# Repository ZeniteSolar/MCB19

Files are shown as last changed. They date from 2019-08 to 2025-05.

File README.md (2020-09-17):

# MCB19






**M**ódulo **C**arregamento das **B**aterias 2019 

Embarcação Guarapuvu II

Equipe Zênite Solar

### LICENSES

- All firmware (unless otherwise noted), [is licensed under GPL-3.0 or any later version](https://www.gnu.org/licenses/gpl.html)
- All hardware is [licensed under CERN-OHL-S v2 or any later version](https://ohwr.org/cern_ohl_s_v2)

### Sobre

Este módulo é responsável por carregar e gerenciar a carga da bateria auxiliar (rádio e bombas de porão) e da bateria extra (direção elétrica) a partir da energia da bateria principal.

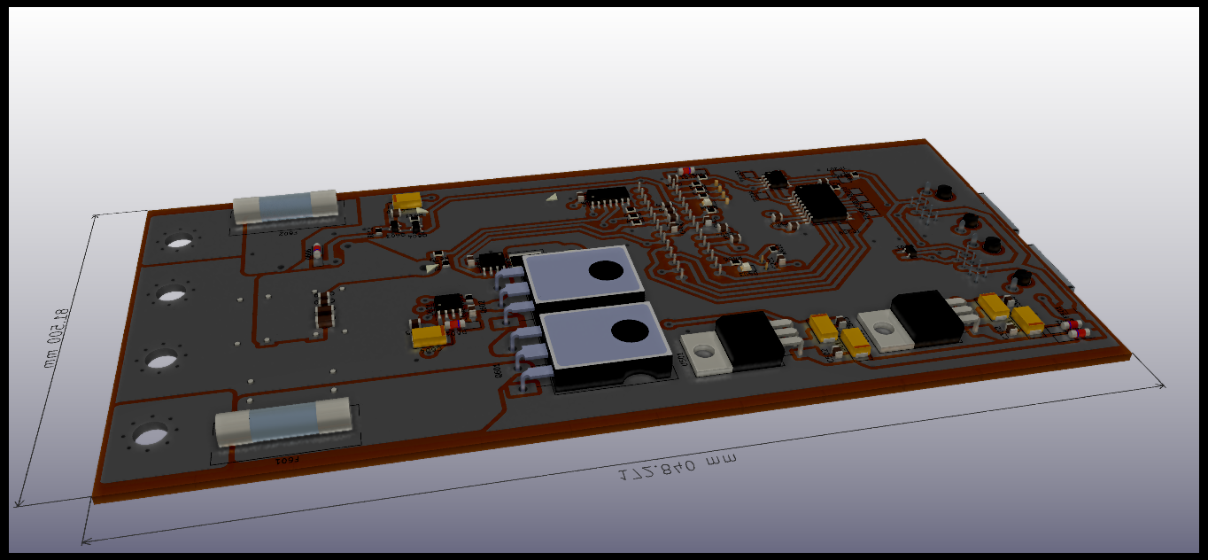
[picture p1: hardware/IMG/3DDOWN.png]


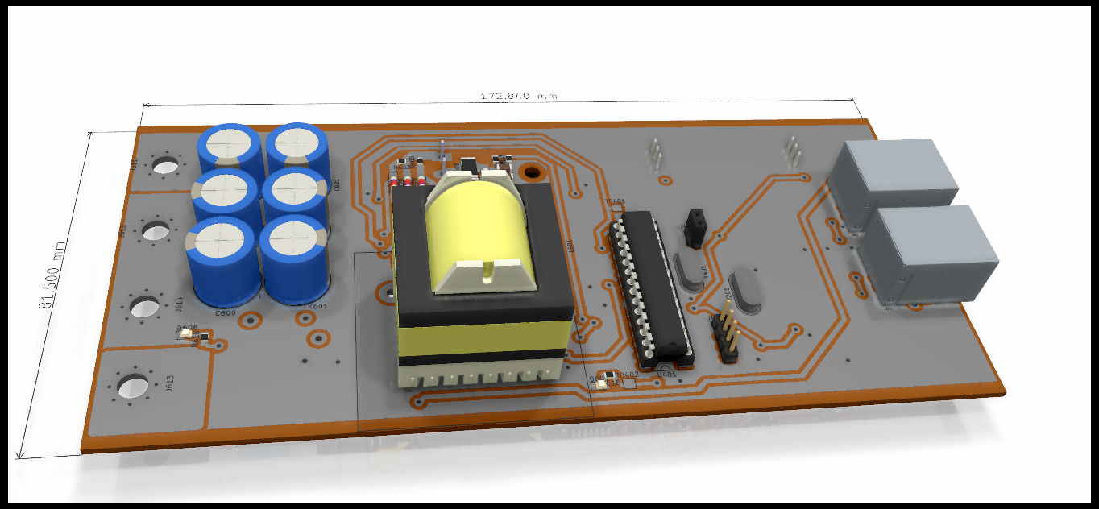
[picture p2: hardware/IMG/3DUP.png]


#### Requisitos

1. Carregar a bateria

   - Carregar por CC e CV
      - Controlar a tensao com controlador PI em cascata com controlador PI de corrente.

   - Proteções
      - Sobrecorrente na entrada e saída
      - Curto-circuito na entrada e saída
      - Sobre/sub-tensão na entrada e saída
      - Não permitir corrente da saída para a entrada: Um relé em série com a carga é usado para permitir a leitura da tensão na saída antes de entregar corrente para ela, seguindo as seguintes regras:
        - Somente ligar o relé da saída quando o sistema estiver em regime (sem oscilações na entrada ou na saída).
        - Somente ligar o relé da saída quando a tensão na bateria estiver em niveis dentro do esperado. 

2. Monitoramento do estado das baterias

   - Enviar pela rede CAN:
      - Corrente de carga
      - Tensão da bateria
      - Tensão da bateria principal
### Abordagens

 1. Especificação do conversor
   - Tensão de entrada: 30-50V
   - Corrente de saida: 8A
   - Tensão de saida: 10-15V

   Como no sistema, a tensão da bateria principal (entrada) será sempre maior que a tensão a tenão da bateria extra/auxiliar (saída), foi escolhido projetar um conversor estatico CC-CC Buck, com chaveamento síncrono (dois mosfets) para maior obter eficiencia.
   #### [Projeto do Buck](https://github.com/ZeniteSolar/MCB19/blob/master/control/buck.ipynb)
   
   - Para as condições especificadas anteriormente foram escolhidos:
      - Capacitor de saida: 200uF
      - Indutor de saida 300uH
 2. Controlador
   - Por sua simplicidade de implementação e por permitir ajustes empíricos, controladores PI foram escolhidos para controlar tanto a tensão de saída quanto a corrente de saída.
   
   [Referencia](https://e2e.ti.com/cfs-file/__key/communityserver-discussions-components-files/902/PI-controller-equations.pdf)
 
 3. Simulações
   - Para a simulação foi usado o programa Psim pois ele oferece a simulação de bloco C onde foi possivel simular de uma forma simplificada o comportamento do atmega328p, alem de ter ferramentas para controle.

<table width="100%">
  <tr>
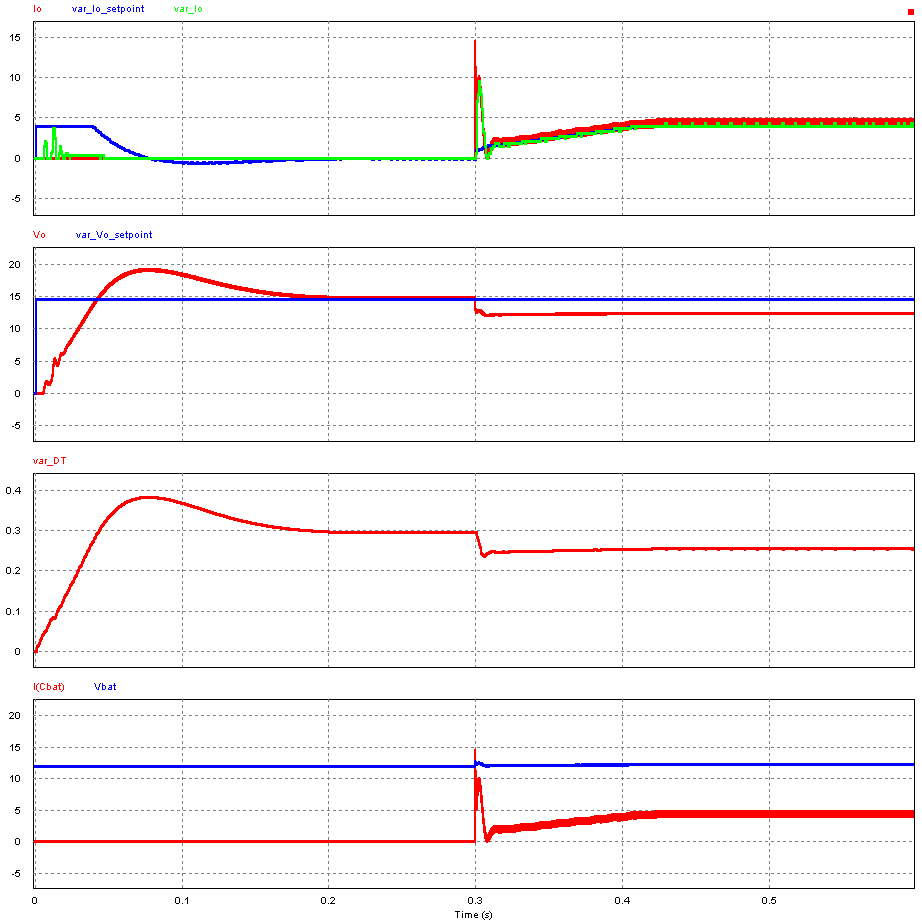
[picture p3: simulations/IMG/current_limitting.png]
    <th width="35%"> </th>
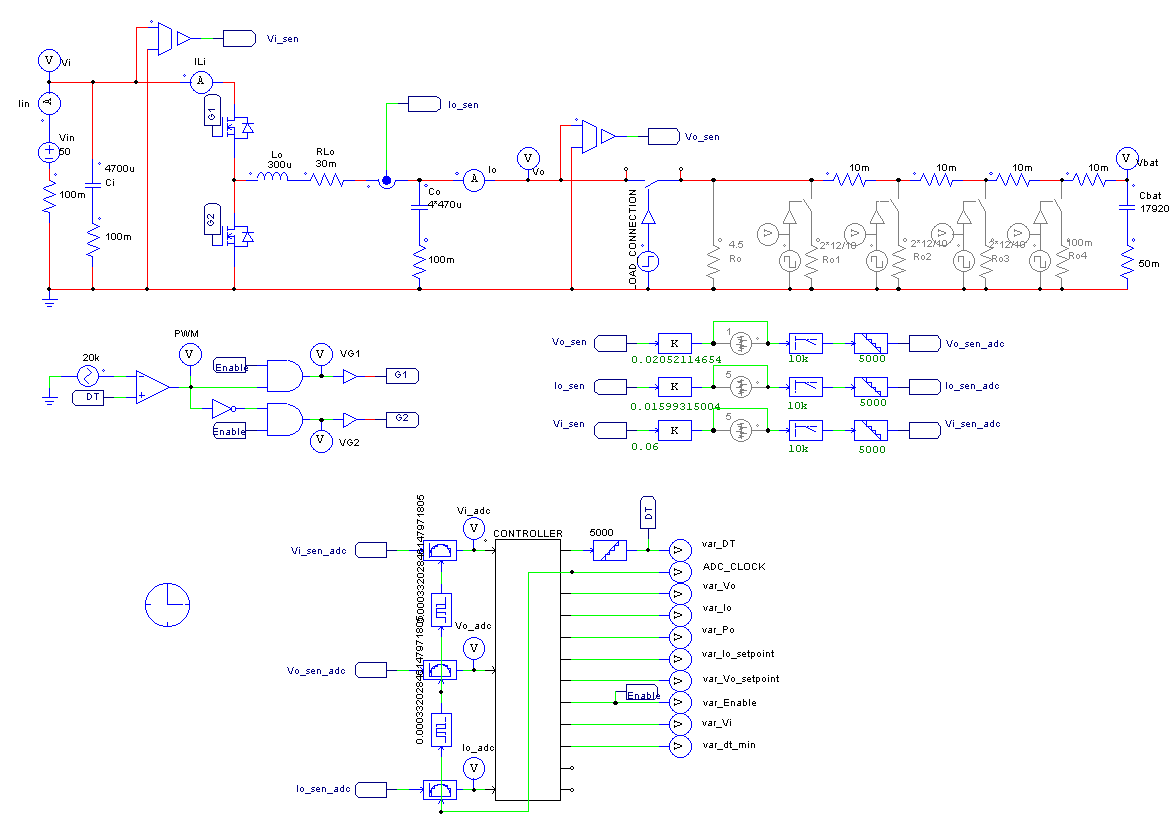
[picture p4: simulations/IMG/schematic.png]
    <th width="65%"></th>
  </tr>
</table>

   4. Hardware
   - Para o design da Placa de circuito impresso (PCB) foi utilizado o software KiCad por ser uma ferramenta OpenSource. A PCB foi fabricada usando transferencia termica.
   
   #### É importante a utilização de snubber para amortecer os picos de tensão nas chaves
   
   5. Firmware
   - A cada interrupção do ADC é chamada a função de controle. Ao finalizar a maquina de estados é executada onde as mensagens CAN são enviadas e recebidas.
   
### [src/conf.h](firmware/src/conf.h)

Configurações gerais do sistema
```C
//#Definições do conversor
#define VO_SETPOINT 	13.2
#define IO_MAX      	8
#define VI_MIN      	21
```
### [src/adc.c](firmware/src/adc.c)
   No arquivo adc.c são lidos os valores dos ADCs e convertidos a valores "humanos", tambem é chamada a função de controle
   - Coeficientes de linearização
      - Com estes coeficientes é convertido o valor lido pelo ADC em uma unidade de medida 
```C
    static const float vi_coeff = 0.06582490575070313f;                                         
    static const float vo_coeff = 0.06717781789490249f;                          
    static const float io_coeff = 0.01599315004f; 
```
### [src/control.c](firmware/src/control.c)
   No arquivo control.c é executado o algoritmo de controle (PiVo em cascata com PiIo), para sintonizar o controlador tem que mudar as constantes Kp e Ti

```C

/*          PI CONTROL ALGORITHM - SERIES IMPLEMENTATION
** /desc    Algoritimo para Controlador Proporcional Integrativo Diferencial.
**  ref1: 
https://e2e.ti.com/cfs-file/__key/communityserver-discussions-components-files/902/PI-controller-equations.pdf

** /var r é o valor desejado para a saída, o 'set-point'.
** /var y é o valor da saída.
** /ret     retorna a ação de controle u.
*/
inline float piVo(float r, float y){
    // PI CONFIGURATIONS:
    const float Kp = 0.5;           // analog series proportional gain
    const float Ti = 0.1;          // analog series integration period
    const float Ts = PERIOD;        // digital sampling period

    // INTERNAL CONSTANTS COMPUTATION:
    const float a0 = -Kp;           // IIR coefficient for old sample
    const float a1 = Kp*(1+Ts/Ti);  // IIR coefficient for new sample

    // CONTROLLER STATIC VARIABLES
    static float e0 = 0;            // old error
    static float e1 = 0;            // new error
    static float u = 0;             // control action

    // Compute error:
    e0 = e1;
    e1 = r -y;

    // Compute control action:
    u += + a1*e1 + a0*e0;

    return u;
}

inline float piIo(float r, float y){
    // PI CONFIGURATIONS:
    const float Kp = 0.001;         // analog series proportional gain
    const float Ti = 0.001;         // analog series integration period
    const float Ts = PERIOD;        // digital sampling period

    // INTERNAL CONSTANTS COMPUTATION:
    const float a0 = -Kp;           // IIR coefficient for old sample
    const float a1 = Kp*(1+Ts/Ti);  // IIR coefficient for new sample

    // CONTROLLER STATIC VARIABLES
    static float e0 = 0;            // old error
    static float e1 = 0;            // new error
    static float u = 0;             // control action

    // Compute error:
    e0 = e1;
    e1 = r -y;

    // Compute control action:
    u += + a1*e1 + a0*e0;

    // Anti windup
    if(u < D_MIN)           u = D_MIN;
    else if(u > D_MAX)      u = D_MAX;

    return u;
}
```
### [src/machine.c](firmware/src/control.c)
   No arquivo machine.c é executada a maquina de estados

```C
inline void machine_run(void)                                                    
{                                                                                   
    if(print_adc){ print_infos(); print_adc = 0;}                                   
                                                                                    
    if(machine_clk){                                                                
        machine_clk = 0;                                                            
                                                                                    
        if(error_flags.all){                                                        
            print_system_flags();                                                   
            print_error_flags();                                                    
            print_infos();                                                          
            set_state_error();                                                      
        }                                                                           
                                                                                    
        switch(state_machine){                                                      
            case STATE_INITIALIZING:                                                
                task_initializing();                                                
                                                                                    
                break;                                                              
            case STATE_IDLE:                                                        
                task_idle();                                                                    
                                                                                    
                break;                                                              
            case STATE_RUNNING:                                                     
                task_running();                                                     
                #ifdef CAN_ON                                                       
                    can_app_task();                                                 
                #endif /* CAN_ON */                                                 
                                                                                    
                break;                                                              
            case STATE_ERROR:                                                       
                task_error();                                                       
                                                                                    
            case STATE_RESET:                                                       
            default:                                                                
                task_reset();                                                       
                break;                                                              
        }                                                                           
    }                                                                               
}                
```

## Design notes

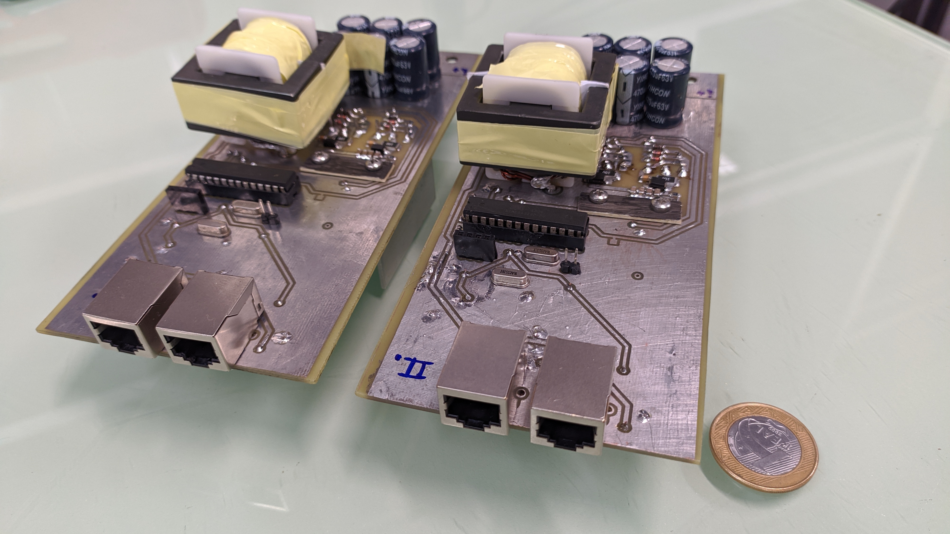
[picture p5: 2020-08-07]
hardware/IMG/PlacaMontada_3.jpg

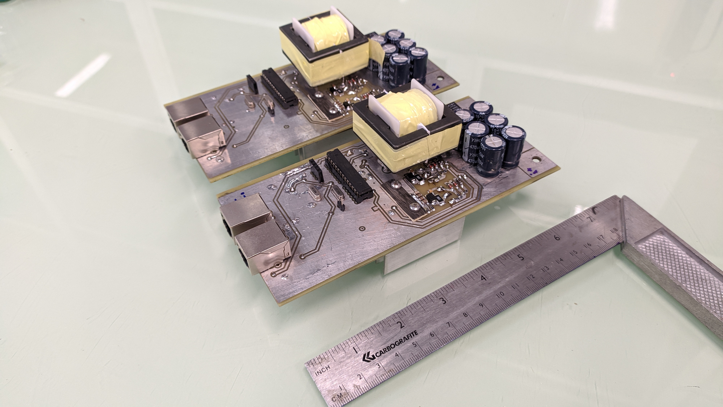
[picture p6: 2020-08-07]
hardware/IMG/PlacaMontada_2.jpg

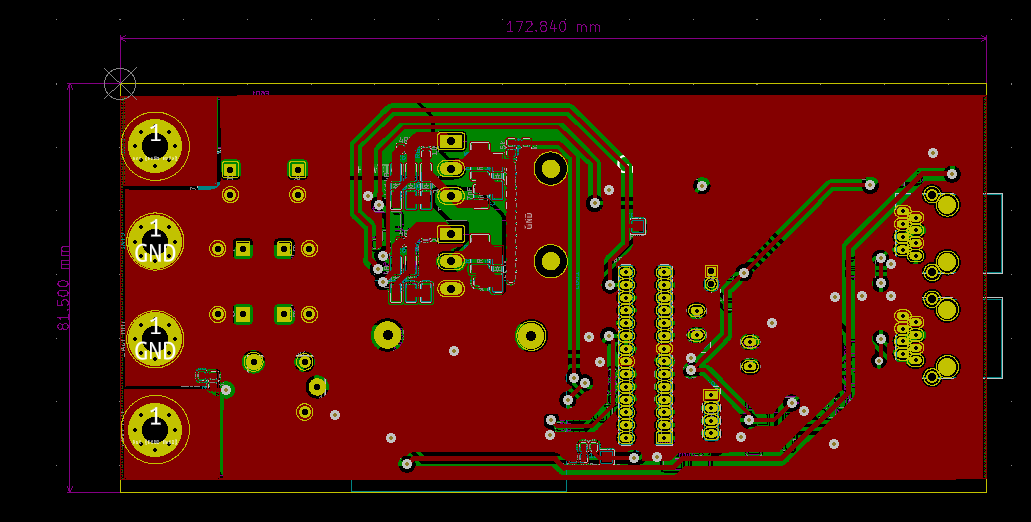
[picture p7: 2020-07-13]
hardware/IMG/layouttop.png

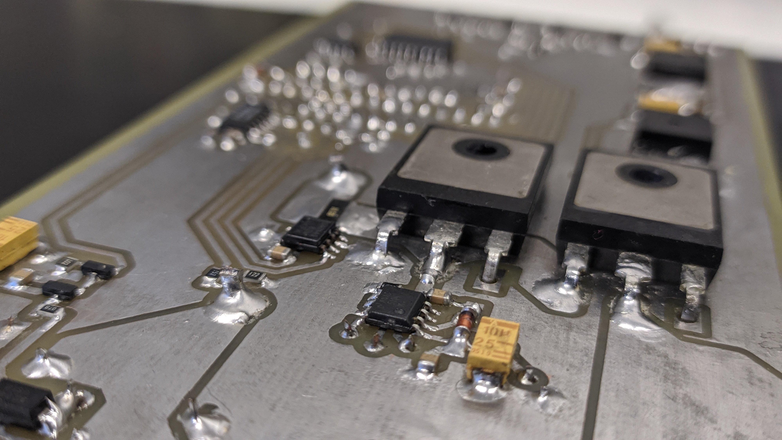
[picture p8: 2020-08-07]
hardware/IMG/PlacaMontadaemdetalhe_DRIVEREMOSFET.jpg

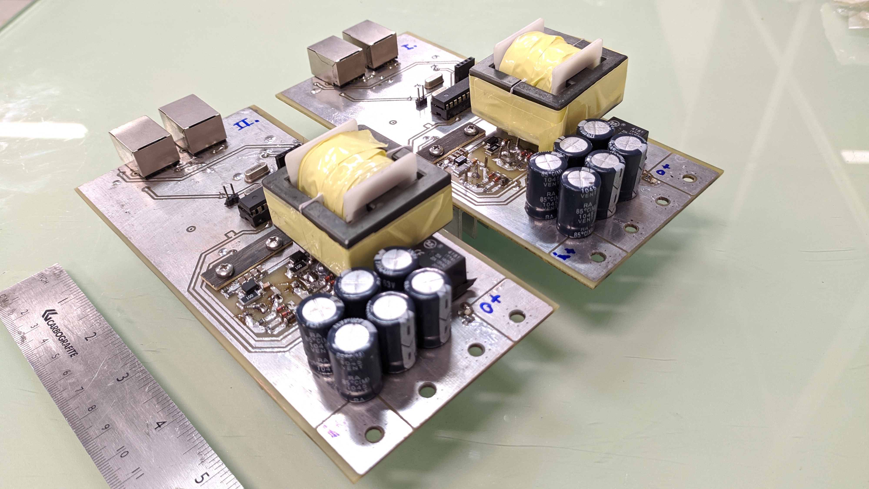
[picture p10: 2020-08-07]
hardware/IMG/PlacaMontada.jpg

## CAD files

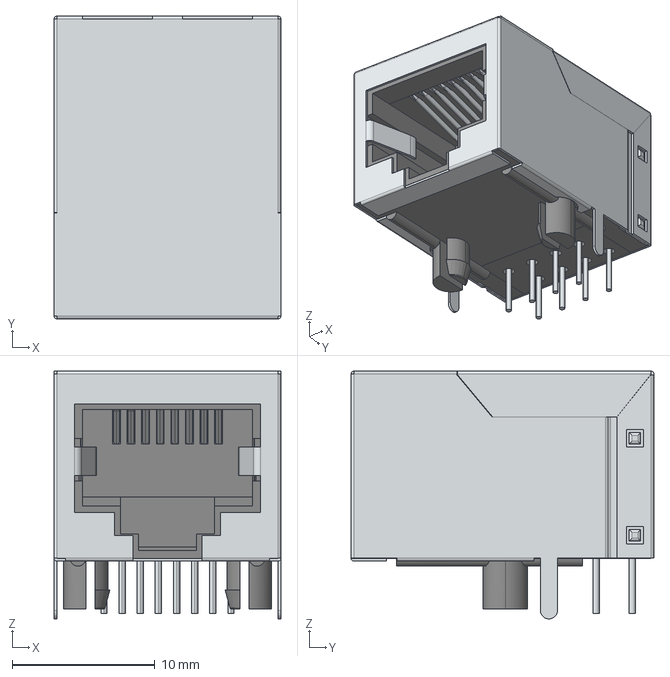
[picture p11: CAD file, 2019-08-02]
hardware/rj45.step
15.9 x 21.2 x 17.3 mm

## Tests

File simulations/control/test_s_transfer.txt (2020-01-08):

C:\users\joaoantoniocardoso\Desktop\ZeniteSolar\2019\MCB19\simulations\control\test_s
C:\users\joaoantoniocardoso\Desktop\ZeniteSolar\2019\MCB19\simulations\control\test_s_param.txt
Loop type = Double
Outer loop = voltage divider + PI
Inner loop = current sensor + PI
Export option = sdomain
Get = Regulator and parameters

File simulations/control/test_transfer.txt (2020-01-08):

C:\users\joaoantoniocardoso\Desktop\ZeniteSolar\2019\MCB19\simulations\control\test.psimsch
C:\users\joaoantoniocardoso\Desktop\ZeniteSolar\2019\MCB19\simulations\control\test_param.txt
Loop type = Double
Outer loop = voltage divider + PI
Inner loop = current sensor + PI
Export option = components
Get = Only parameters

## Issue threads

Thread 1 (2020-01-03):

PWM pin

guilhermecv, 2020-01-03:
Alterar pino do PWM, atualmente no PC5

joaoantoniocardoso, 2020-01-08:
Nesse protótipo está no PB2, mas ainda não foi alterado no esquemático e layout.

Closed 2020-01-22.

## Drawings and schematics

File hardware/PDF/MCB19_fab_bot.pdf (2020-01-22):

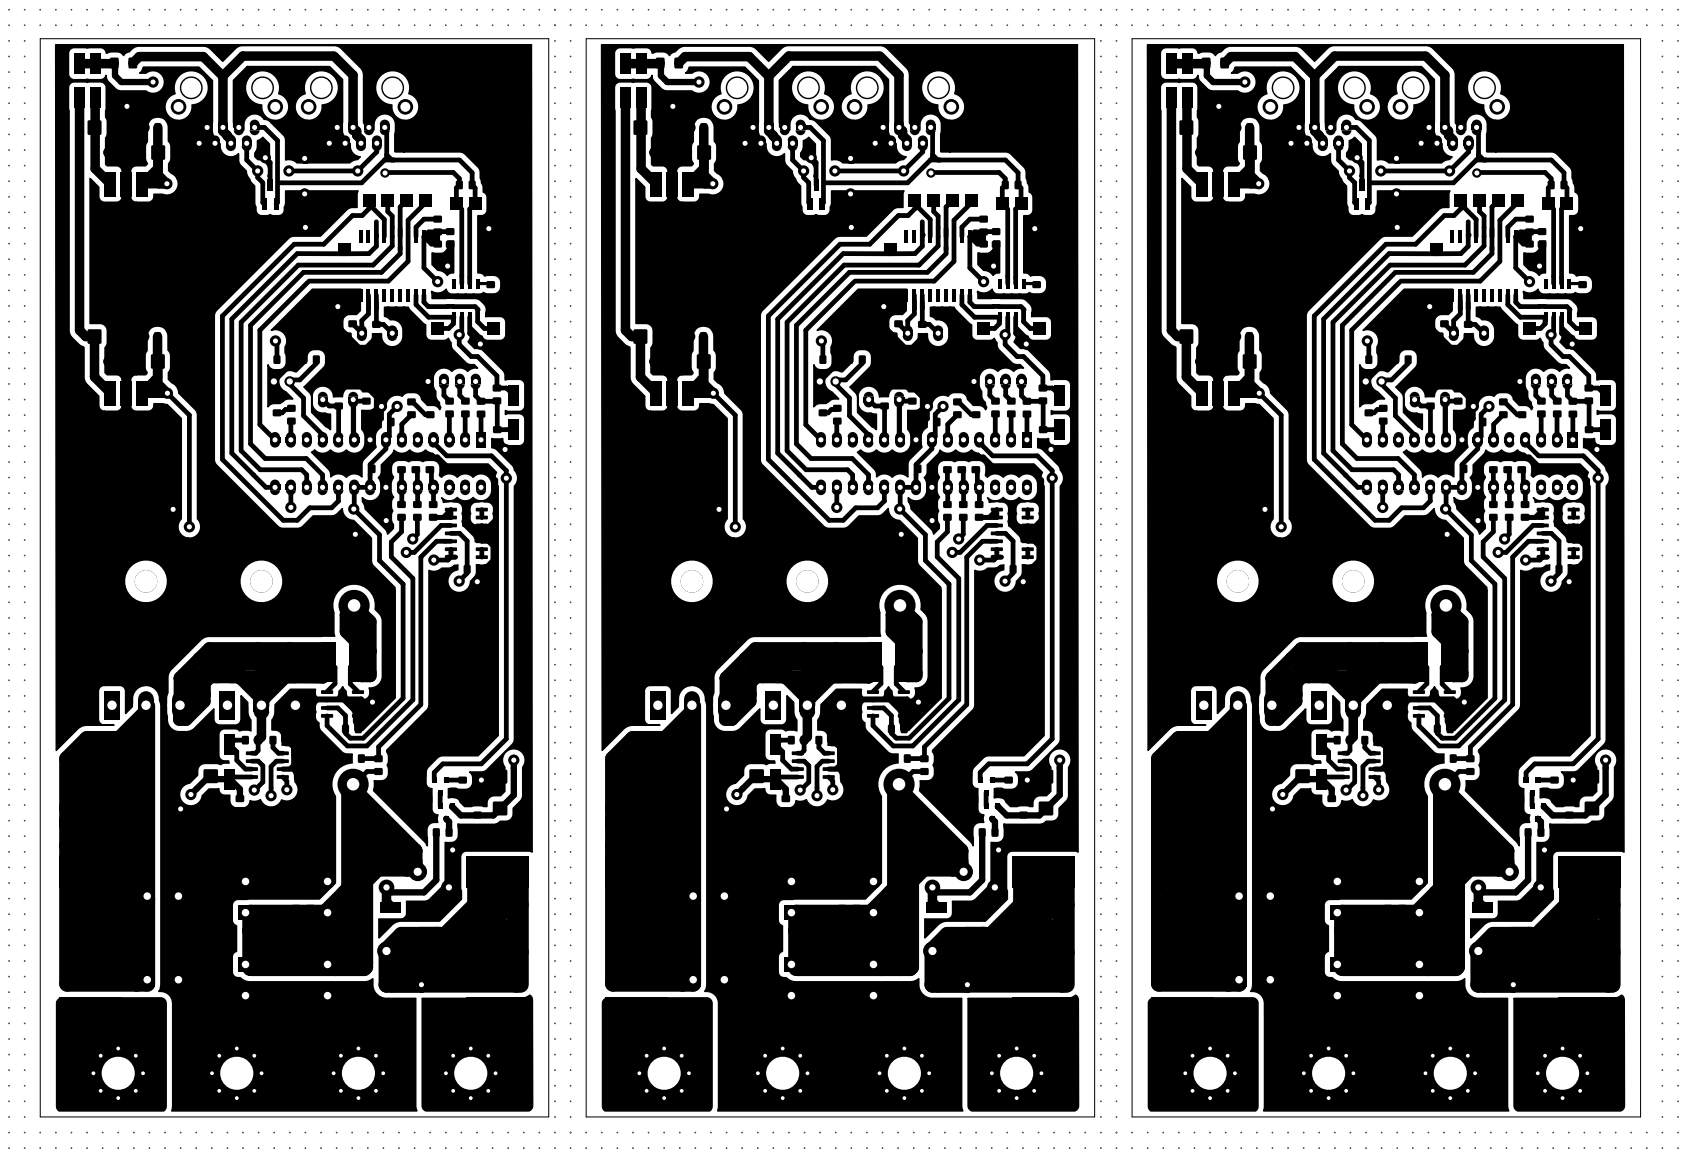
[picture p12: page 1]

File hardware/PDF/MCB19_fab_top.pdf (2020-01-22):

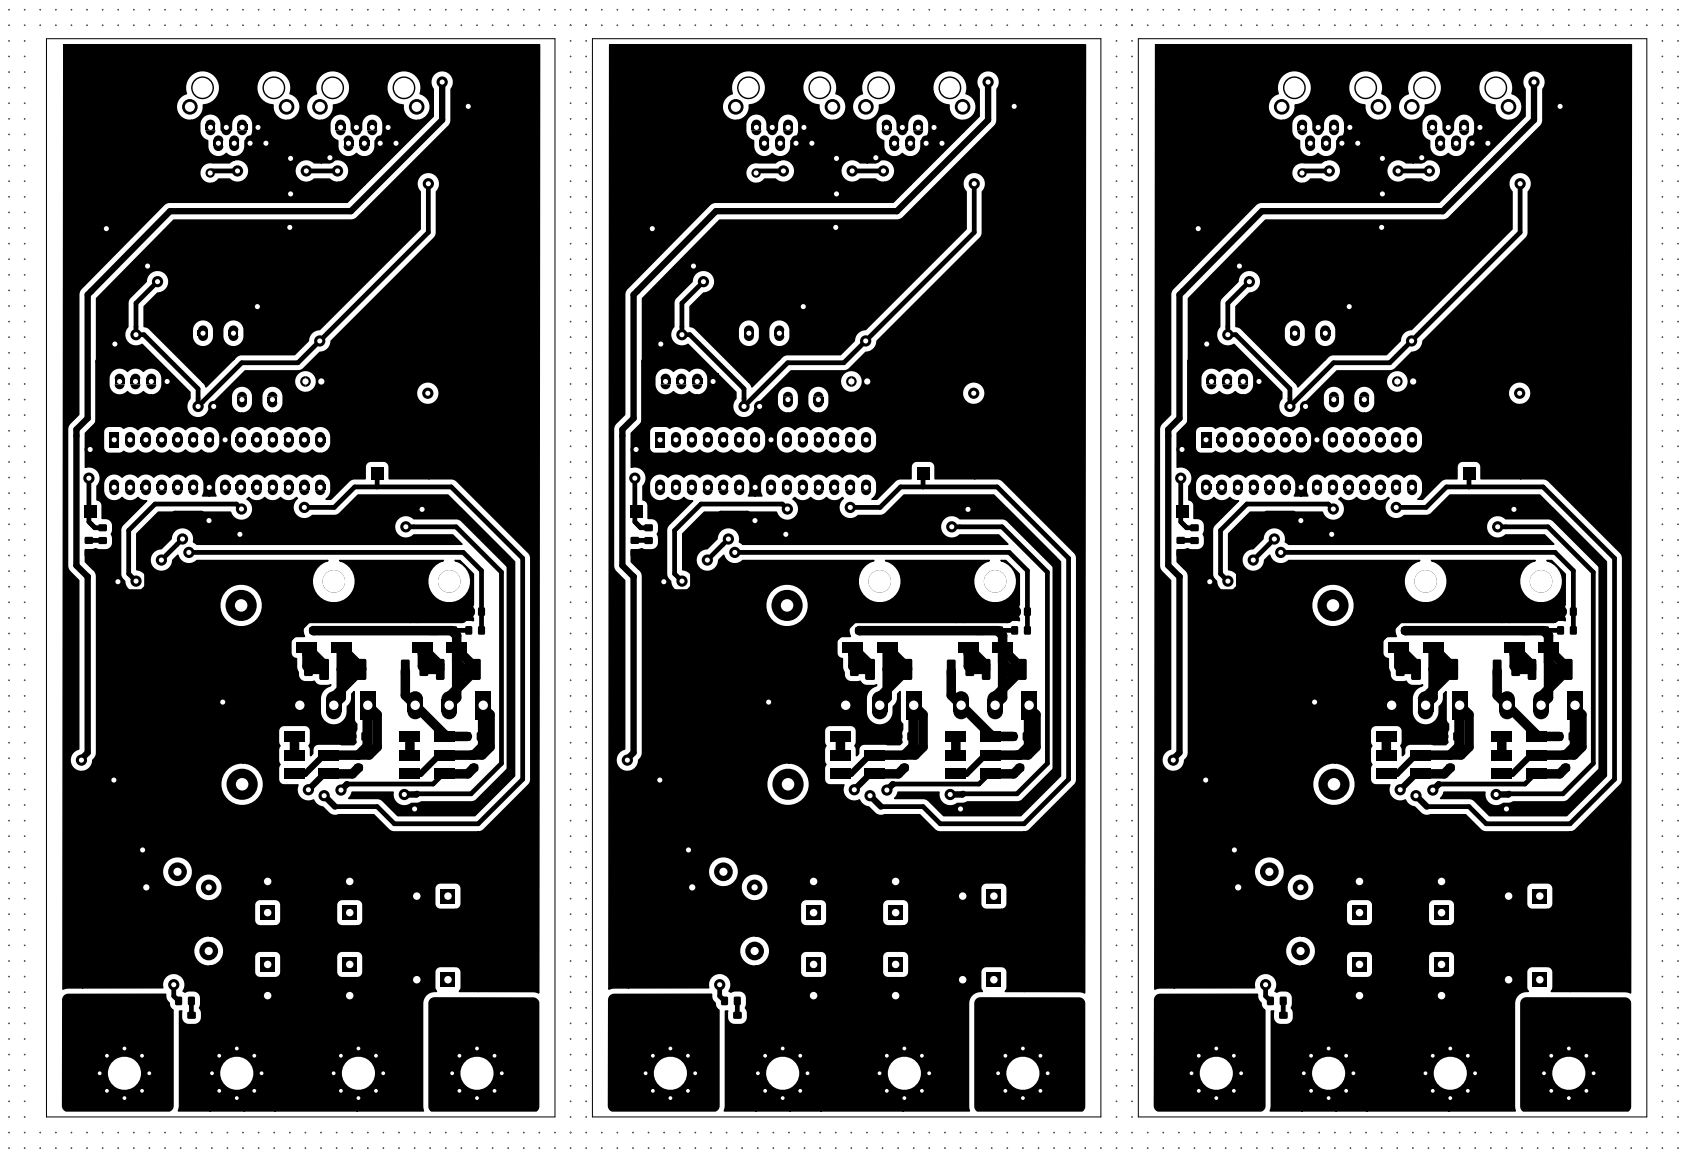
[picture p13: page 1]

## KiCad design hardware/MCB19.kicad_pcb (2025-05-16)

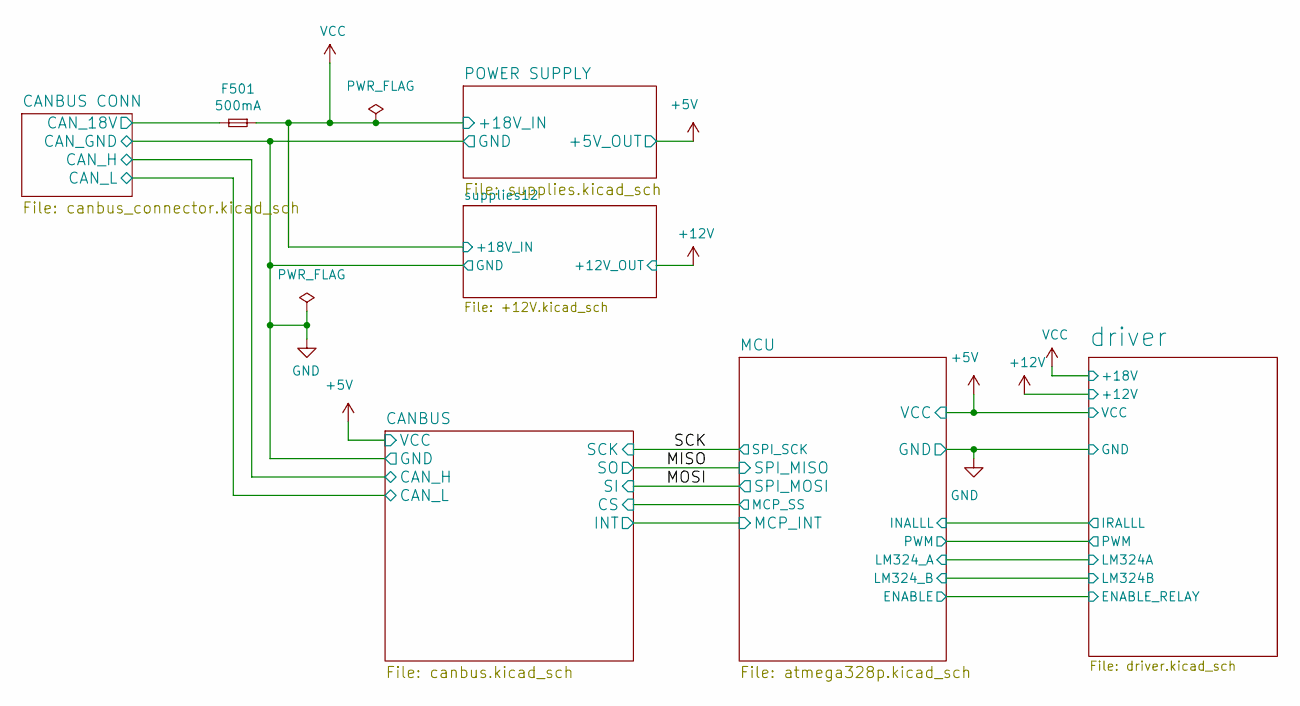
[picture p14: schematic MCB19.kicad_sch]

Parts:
F501: 500mA; Fuse_1206_3216Metric_Pad1.42x1.75mm_HandSolder

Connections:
/CANBUS CONN/CAN_18V: F501.2; also elsewhere on the board
VCC: F501.1; also elsewhere on the board

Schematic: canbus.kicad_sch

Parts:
C201, C202, C205: 100nF; C_0805_2012Metric_Pad1.15x1.40mm_HandSolder
C203, C204: 22pF; C_0805_2012Metric_Pad1.15x1.40mm_HandSolder
D201: pesd1can; SOT-23_Handsoldering
R201: 1k; R_0805_2012Metric_Pad1.15x1.40mm_HandSolder
R202: 4k7; R_0805_2012Metric_Pad1.15x1.40mm_HandSolder
R203: 10k; R_0805_2012Metric_Pad1.15x1.40mm_HandSolder
TP201: SI; TestPoint_Pad_2.0x2.0mm
TP202: SO; TestPoint_Pad_2.0x2.0mm
TP203: TXCAN; TestPoint_Pad_2.0x2.0mm
TP204: RXCAN; TestPoint_Pad_2.0x2.0mm
TP205: SC; TestPoint_Pad_2.0x2.0mm
TP206: SCK; TestPoint_Pad_2.0x2.0mm
TP207: CAN_H; TestPoint_Pad_2.0x2.0mm
TP208: CAN_L; TestPoint_Pad_2.0x2.0mm
TP209: INT; TestPoint_Pad_2.0x2.0mm
U201: MCP2551-I/SN; SOIC-8_3.9x4.9mm_P1.27mm
U202: MCP2515-xSO; SOIC-18W_7.5x11.6mm_P1.27mm
Y201: 16MHz; Crystal_HC49-U_Vertical

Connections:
+5V: C201.1, C202.1, C205.1, R203.1, U201.3 (VDD), U202.18 (VDD); also elsewhere on the board
/CANBUS CONN/CAN_H: D201.1, R201.2, TP207.1, U201.7 (CANH); also elsewhere on the board
/CANBUS CONN/CAN_L: D201.2, R201.1, TP208.1, U201.6 (CANL); also elsewhere on the board
/CANBUS/RXCAN: TP204.1, U201.4 (RXD), U202.2 (RXCAN)
/CANBUS/TXCAN: TP203.1, U201.1 (TXD), U202.1 (TXCAN)
/MCU/MCP_INT: TP209.1, U202.12 (~INT); also elsewhere on the board
/MCU/MCP_SS: TP205.1, U202.16 (~CS); also elsewhere on the board
/MISO: TP202.1, U202.15 (SO); also elsewhere on the board
/MOSI: TP201.1, U202.14 (SI); also elsewhere on the board
/SCK: TP206.1, U202.13 (SCK); also elsewhere on the board
unnamed: R202.1, U201.8 (STBY)
unnamed: C204.1, U202.8 (OSC1), Y201.2
unnamed: C203.1, U202.7 (OSC2), Y201.1
unnamed: R203.2, U202.17 (~RESET)

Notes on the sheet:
EMI/ESD Protection Solutions for the CAN Bus: https://www.onsemi.com/pub/Collateral/AND8169-D.PDF SparkFun CAN-Bus Shield: https://cdn.sparkfun.com/datasheets/Dev/Arduino/Shields/SparkFun_CAN-Bus_Shield_v13a.pdf

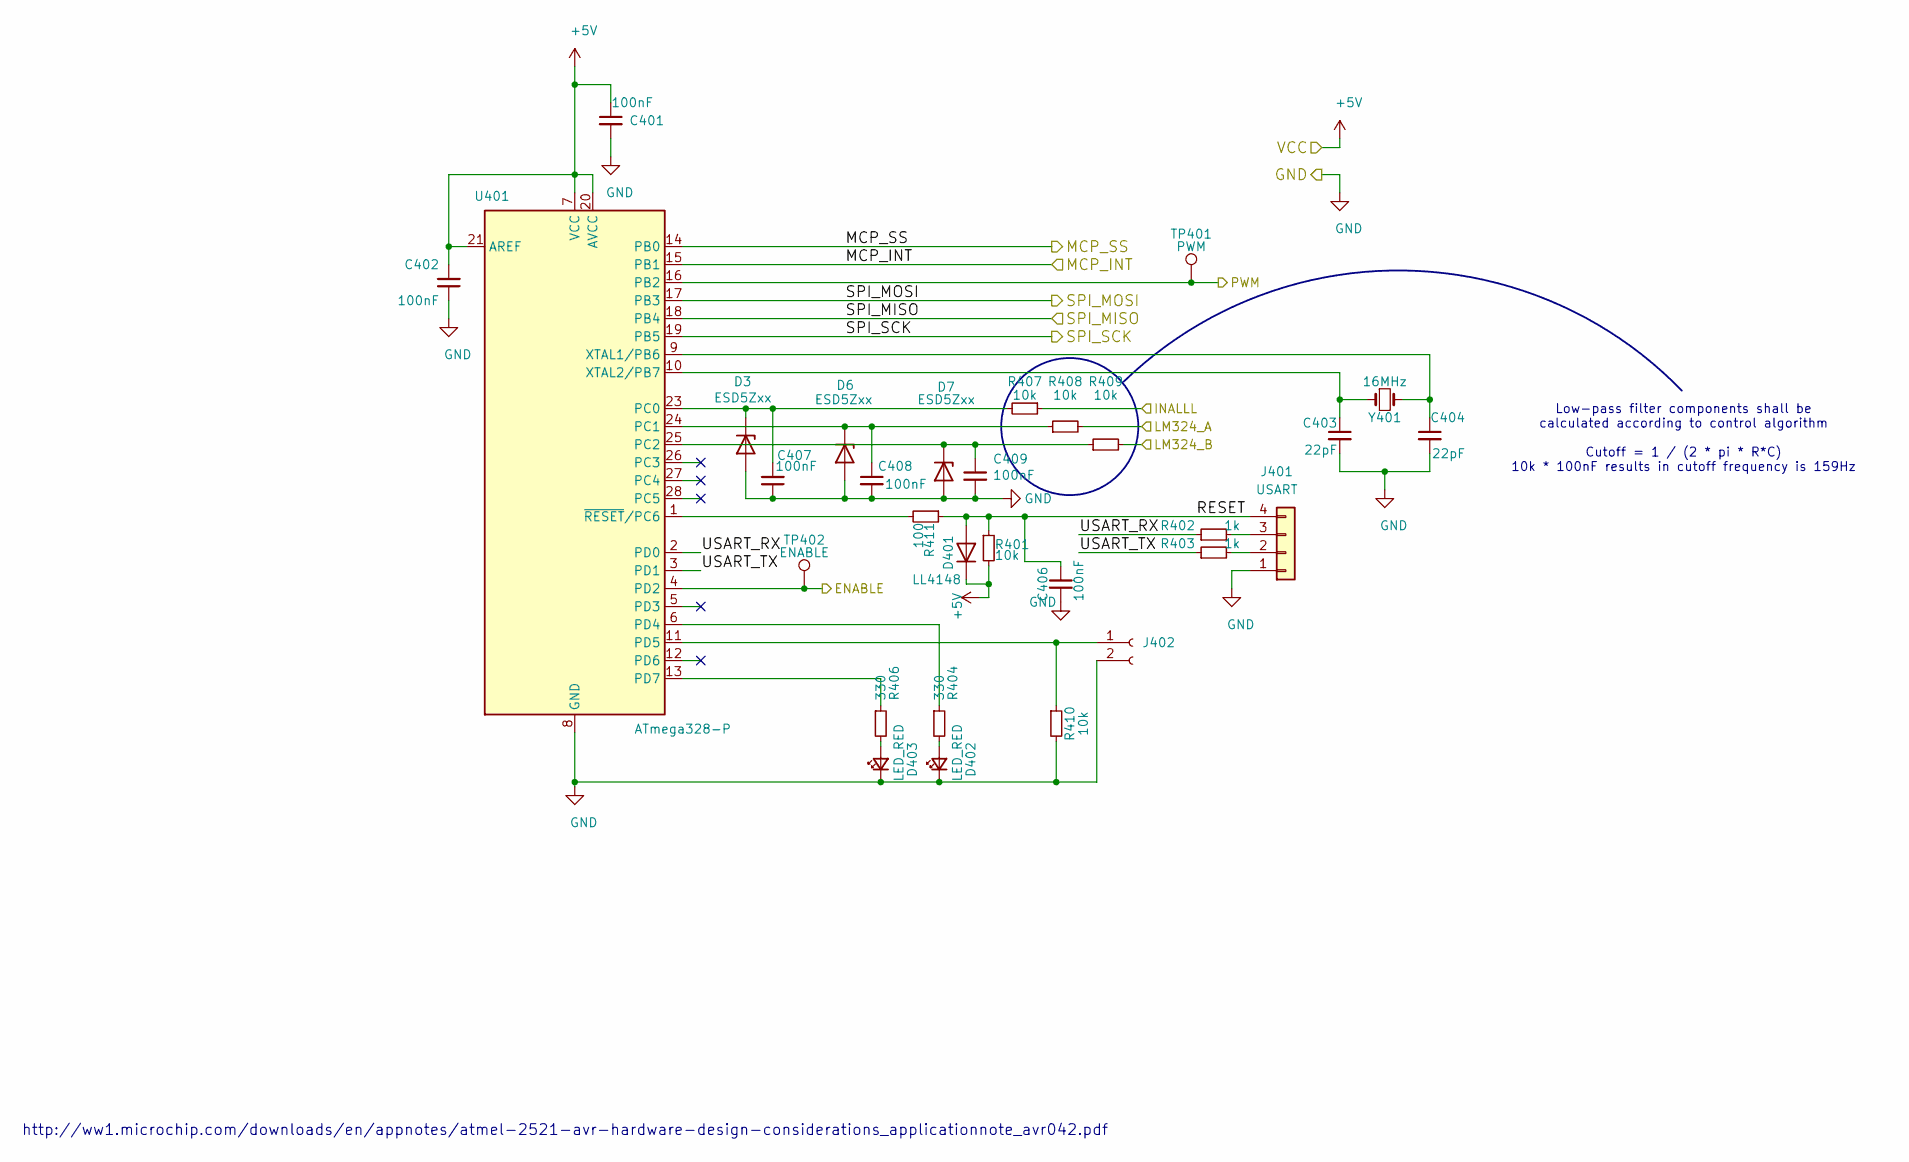
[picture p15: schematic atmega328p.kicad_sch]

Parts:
C401, C402, C406, C407, C408, C409: 100nF; C_0805_2012Metric_Pad1.15x1.40mm_HandSolder
C403, C404: 22pF; C_0805_2012Metric_Pad1.15x1.40mm_HandSolder
D3, D6, D7: ESD5Zxx; D_SOD-523
D401: LL4148; D_MiniMELF_Handsoldering
D402, D403: LED_RED; LED_0805_2012Metric_Pad1.15x1.40mm_HandSolder
J401: USART; PinHeader_1x04_P2.54mm_Vertical
J402: Conn_01x02_Socket; PinSocket_1x02_P2.54mm_Vertical
R401, R407, R408, R409, R410: 10k; R_0805_2012Metric_Pad1.15x1.40mm_HandSolder
R402, R403: 1k; R_0805_2012Metric_Pad1.15x1.40mm_HandSolder
R404, R406: 330; R_0805_2012Metric_Pad1.15x1.40mm_HandSolder
R411: 100; R_0805_2012Metric_Pad1.15x1.40mm_HandSolder
TP401: PWM; TestPoint_Pad_2.0x2.0mm
TP402: ENABLE; TestPoint_Pad_2.0x2.0mm
U401: ATmega328-P; DIP-28_W7.62mm_LongPads
Y401: 16MHz; Crystal_HC49-U_Vertical

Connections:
+5V: C401.1, C402.2, D401.1 (K), R401.2, U401.7 (VCC), U401.20 (AVCC), U401.21 (AREF); also elsewhere on the board
/MCU/ENABLE: TP402.1, U401.4 (PD2); also elsewhere on the board
/MCU/INALLL: R407.1; also elsewhere on the board
/MCU/LM324_A: R408.2; also elsewhere on the board
/MCU/LM324_B: R409.2; also elsewhere on the board
/MCU/MCP_INT: U401.15 (PB1); also elsewhere on the board
/MCU/MCP_SS: U401.14 (PB0); also elsewhere on the board
/MCU/PWM: TP401.1, U401.16 (PB2); also elsewhere on the board
/MCU/RESET: C406.1, D401.2 (A), J401.4, R401.1, R411.1
/MCU/USART_RX: R402.1, U401.2 (PD0)
/MCU/USART_TX: R403.1, U401.3 (PD1)
/MISO: U401.18 (PB4); also elsewhere on the board
/MOSI: U401.17 (PB3); also elsewhere on the board
/SCK: U401.19 (PB5); also elsewhere on the board
unnamed: C407.2, D3.1 (K), R407.2, U401.23 (PC0)
unnamed: C408.1, D6.1 (K), R408.1, U401.24 (PC1)
unnamed: C409.1, D7.1 (K), R409.1, U401.25 (PC2)
unnamed: D402.2 (A), R404.2
unnamed: D403.2 (A), R406.2
unnamed: J401.2, R403.2
unnamed: J401.3, R402.2
unnamed: J402.1, R410.1, U401.11 (PD5)
unnamed: R404.1, U401.6 (PD4)
unnamed: R406.1, U401.13 (PD7)
unnamed: C404.1, U401.9 (XTAL1/PB6), Y401.2
unnamed: C403.1, U401.10 (XTAL2/PB7), Y401.1
unnamed: R411.2, U401.1 (~RESET/PC6)

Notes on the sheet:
http://ww1.microchip.com/downloads/en/appnotes/atmel-2521-avr-hardware-design-considerations_applicationnote_avr042.pdf
Low-pass filter components shall be calculated according to control algorithm Cutoff = 1 / (2 * pi * R*C) 10k * 100nF results in cutoff frequency is 159Hz

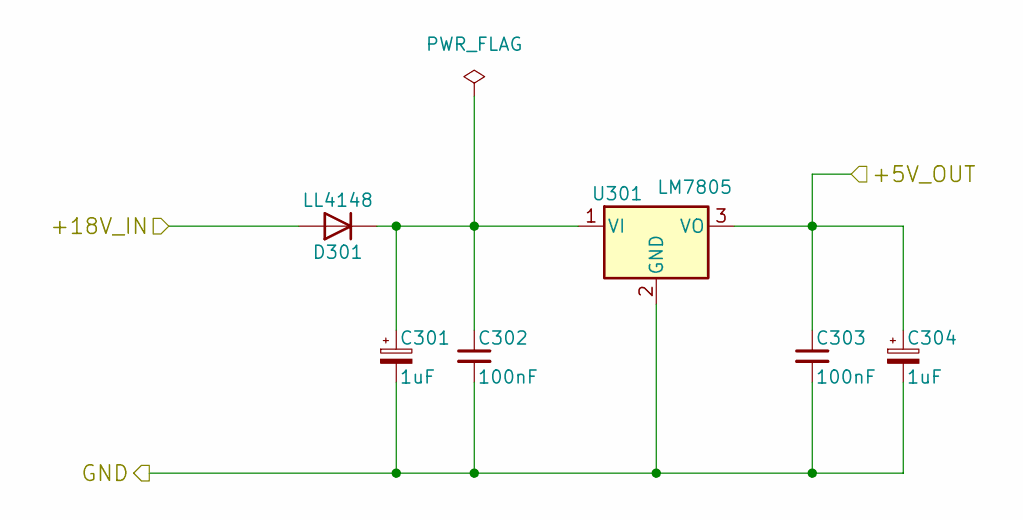
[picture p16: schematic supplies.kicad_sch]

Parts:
C301, C304: 1uF; CP_EIA-6032-20_AVX-F_Pad2.25x2.35mm_HandSolder
C302, C303: 100nF; C_0805_2012Metric_Pad1.15x1.40mm_HandSolder
D301: LL4148; D_MiniMELF_Handsoldering
U301: LM7805; TO-220-3_Horizontal_TabDown_SMD

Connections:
+5V: C303.1, C304.1, U301.3 (VO); also elsewhere on the board
unnamed: C301.1, C302.1, D301.1 (K), U301.1 (VI)
VCC: D301.2 (A); also elsewhere on the board

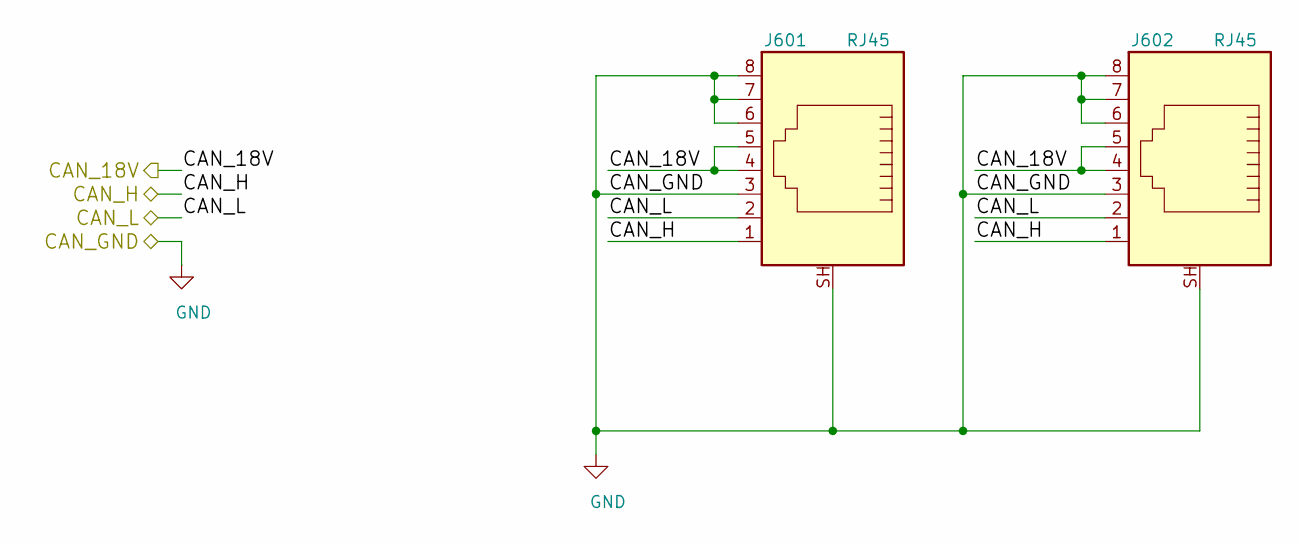
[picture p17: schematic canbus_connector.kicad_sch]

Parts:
J601, J602: RJ45; RJ45_YH59_01

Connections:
/CANBUS CONN/CAN_18V: J601.4, J601.5, J602.4, J602.5; also elsewhere on the board
/CANBUS CONN/CAN_H: J601.1, J602.1; also elsewhere on the board
/CANBUS CONN/CAN_L: J601.2, J602.2; also elsewhere on the board

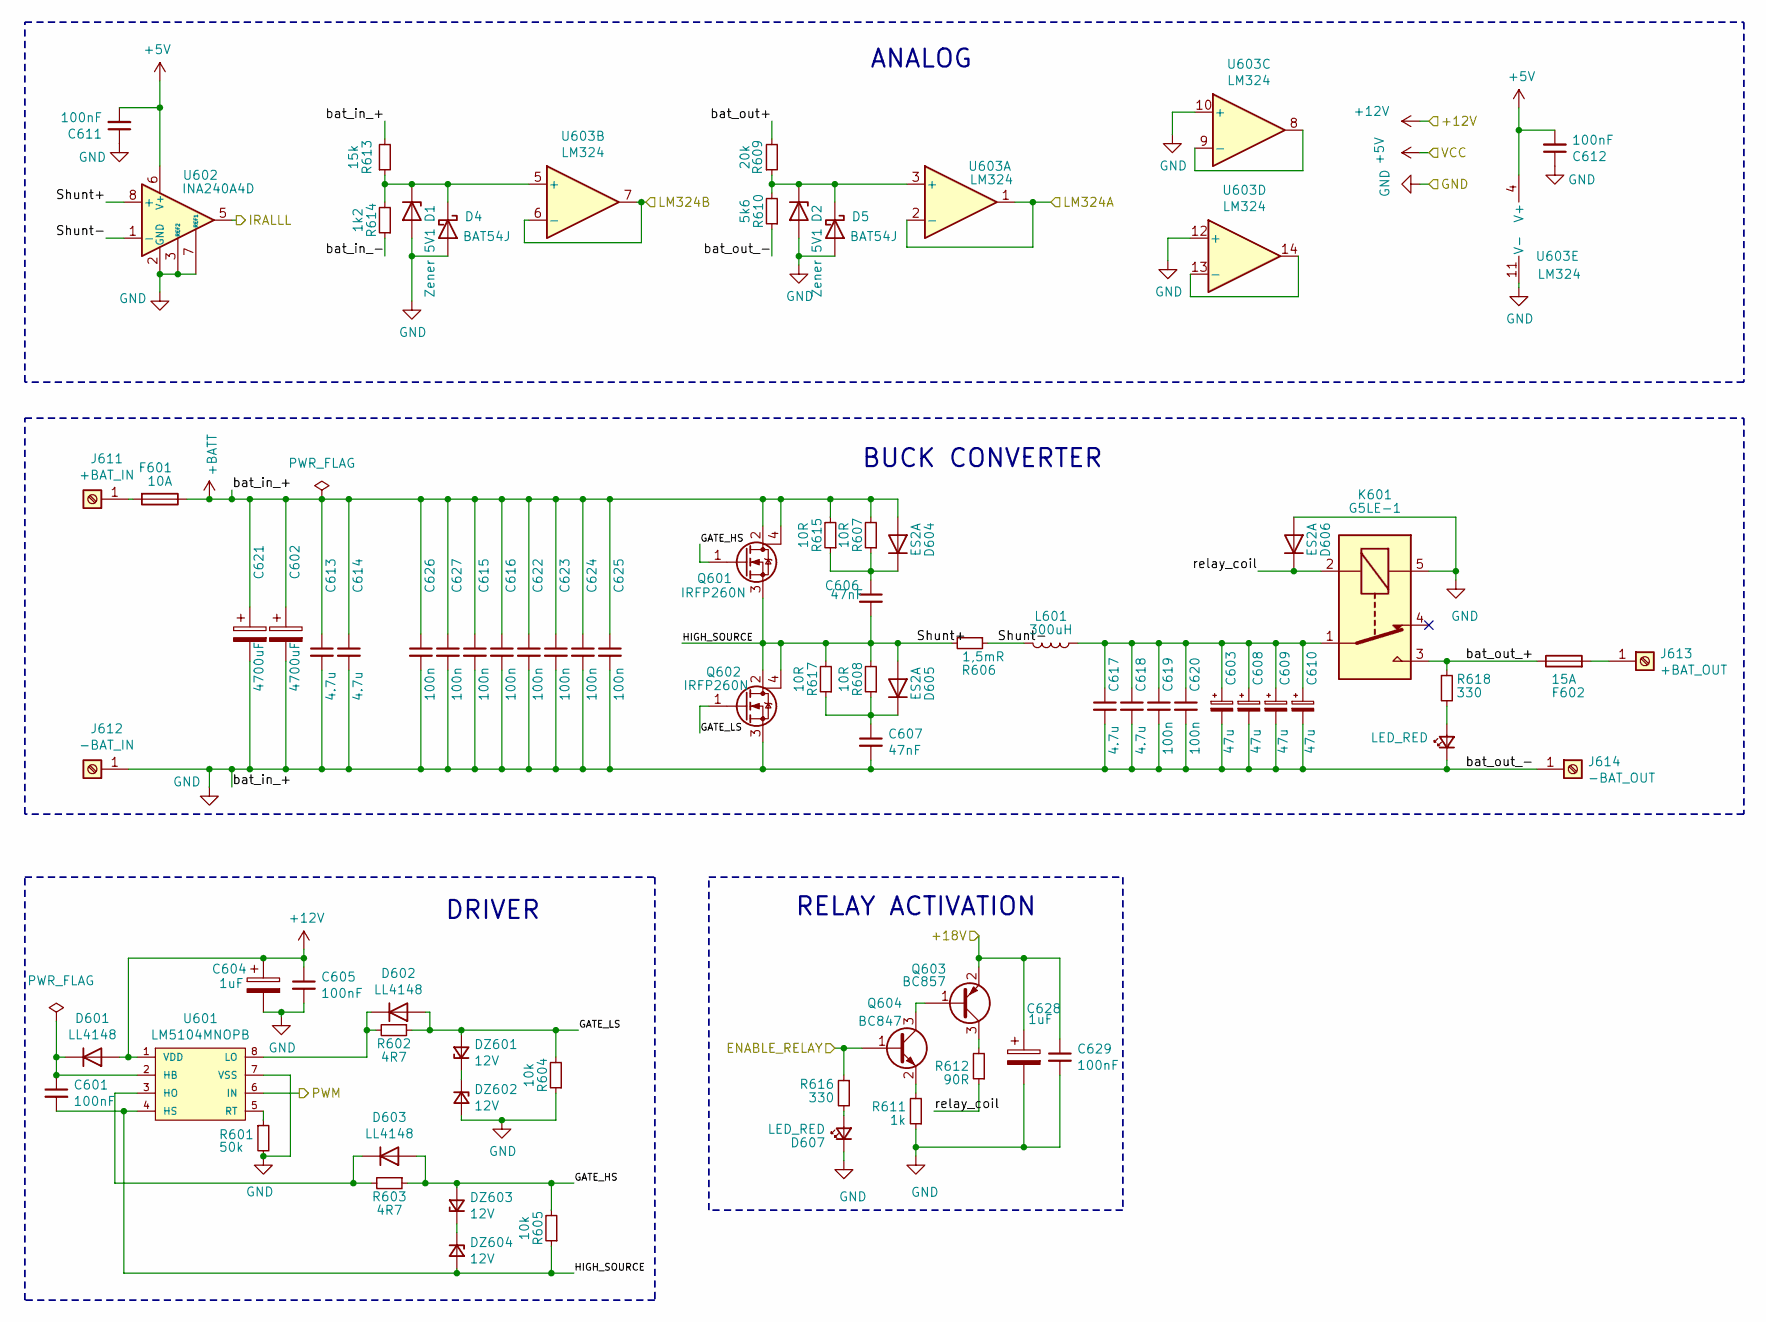
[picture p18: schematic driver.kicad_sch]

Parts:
C601, C605, C611, C612, C629: 100nF; C_0805_2012Metric_Pad1.15x1.40mm_HandSolder
C602, C621: 4700uF; CP_Radial_D12.5mm_P5.00mm
C603, C608, C609, C610: 47u
C604, C628: 1uF; CP_EIA-6032-20_AVX-F_Pad2.25x2.35mm_HandSolder
C606, C607: 47nF; C_1210_3225Metric_Pad1.42x2.65mm_HandSolder
C613, C614, C617, C618: 4.7u; C_1206_3216Metric_Pad1.42x1.75mm_HandSolder
C615, C616, C620, C622, C623, C624, C625, C626, C627: 100n; C_0805_2012Metric_Pad1.15x1.40mm_HandSolder
C619: 100n; C_0805_2012Metric_Pad1.18x1.45mm_HandSolder
D1, D2: Zener 5V1; D_MiniMELF
D4, D5: BAT54J; D_SOD-323F
D601, D602, D603: LL4148; D_MiniMELF_Handsoldering
D604, D605, D606: ES2A; D_MiniMELF_Handsoldering
D607, D608: LED_RED; LED_0805_2012Metric_Pad1.15x1.40mm_HandSolder
DZ601, DZ602, DZ603, DZ604: 12V; D_MiniMELF_Handsoldering
F601: 10A; Fuseholder_Cylinder-5x20mm_Stelvio-Kontek_PTF78_Horizontal_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
F602: 15A; Fuseholder_Cylinder-5x20mm_Stelvio-Kontek_PTF78_Horizontal_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
J611: +BAT_IN; MountingHole_5.3mm_M5_Pad_Via
J612: -BAT_IN; MountingHole_5.3mm_M5_Pad_Via
J613: +BAT_OUT; MountingHole_5.3mm_M5_Pad_Via
J614: -BAT_OUT; MountingHole_5.3mm_M5_Pad_Via
K601: G5LE-1; Relay_SPDT_SANYOU_SRD_Series_Form_C
L601: 300uH; Inductor_Nocoupled
Q601, Q602: IRFP260N; TO-247-3_Horizontal_TabUp
Q603: BC857; SOT-23
Q604: BC847; SOT-23
R601: 50k; R_0805_2012Metric_Pad1.15x1.40mm_HandSolder
R602, R603: 4R7; R_0805_2012Metric_Pad1.15x1.40mm_HandSolder
R604, R605: 10k; R_0805_2012Metric_Pad1.15x1.40mm_HandSolder
R606: 1,5mR; R_2512_6432Metric_Reversed
R607, R615: 10R; R_2512_6332Metric
R608, R617: 10R; R_2512_6332Metric_Pad1.52x3.35mm_HandSolder
R609: 20k; C_0805_2012Metric_Pad1.18x1.45mm_HandSolder
R610: 5k6; R_0805_2012Metric_Pad1.15x1.40mm_HandSolder
R611: 1k; R_0805_2012Metric_Pad1.15x1.40mm_HandSolder
R612: 90R; R_0805_2012Metric_Pad1.15x1.40mm_HandSolder
R613: 15k; R_0805_2012Metric_Pad1.15x1.40mm_HandSolder
R614: 1k2; R_0805_2012Metric_Pad1.15x1.40mm_HandSolder
R616, R618: 330; R_0805_2012Metric_Pad1.15x1.40mm_HandSolder
U601: LM5104MNOPB; SOIC-8_3.9x4.9mm_P1.27mm
U602: INA240A4D; SOIC-8_3.9x4.9mm_P1.27mm
U603: LM324; SOIC-14_3.9x8.7mm_P1.27mm

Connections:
+5V: C611.2, C612.2, U602.6 (V+), U603.4 (V+); also elsewhere on the board
+12V: C604.1, C605.1, D601.2 (A), U601.1 (VDD); also elsewhere on the board
/MCU/ENABLE: Q604.1 (B), R616.1; also elsewhere on the board
/MCU/INALLL: U602.5; also elsewhere on the board
/MCU/LM324_A: U603.1, U603.2 (-); also elsewhere on the board
/MCU/LM324_B: U603.6 (-), U603.7; also elsewhere on the board
/MCU/PWM: U601.6 (IN); also elsewhere on the board
/driver/GATE_HS: D603.2 (A), DZ603.2 (A), Q601.1 (G), R603.1, R605.2
/driver/GATE_LS: D602.2 (A), DZ601.2 (A), Q602.1 (G), R602.1, R604.2
/driver/HIGH_SOURCE: C601.2, C606.2, D605.2 (A), DZ604.2 (A), Q601.3 (S), Q602.2 (D), Q602.4 (D), R605.1, R606.2, R608.2, R617.2, U601.4 (HS), U602.8 (+)
/driver/Shunt-: L601.1, R606.1, U602.1 (-)
/driver/bat_in_-: R614.1
/driver/bat_out+: R609.2
/driver/bat_out_+: F602.1, K601.3, R618.1
/driver/relay_coil: D606.1 (K), K601.2, R612.1
unnamed: C603.1, C608.1, C609.1, C610.1, C617.1, C618.1, C619.1, C620.1, K601.1, L601.2
unnamed: D1.1 (K), D4.1 (K), R613.1, R614.2, U603.5 (+)
unnamed: D2.1 (K), D5.1 (K), R609.1, R610.2, U603.3 (+)
unnamed: C601.1, D601.1 (K), U601.2 (HB)
unnamed: D602.1 (K), R602.2, U601.8 (LO)
unnamed: D603.1 (K), R603.2, U601.3 (HO)
unnamed: C606.1, D604.1 (K), R607.1, R615.1
unnamed: C607.1, D605.1 (K), R608.1, R617.1
unnamed: D607.2 (A), R616.2
unnamed: D608.2 (A), R618.2
unnamed: DZ601.1 (K), DZ602.1 (K)
unnamed: DZ603.1 (K), DZ604.1 (K)
unnamed: F601.2, J611.1
unnamed: F602.2, J613.1
unnamed: Q603.1 (B), Q604.3 (C)
unnamed: Q603.3 (C), R612.2
unnamed: Q604.2 (E), R611.2
unnamed: R601.1, U601.5 (RT)
unnamed: U603.8, U603.9 (-)
unnamed: U603.13 (-), U603.14
VCC: C628.1, C629.1, Q603.2 (E); also elsewhere on the board

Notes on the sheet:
DRIVER
ANALOG
BUCK CONVERTER
RELAY ACTIVATION

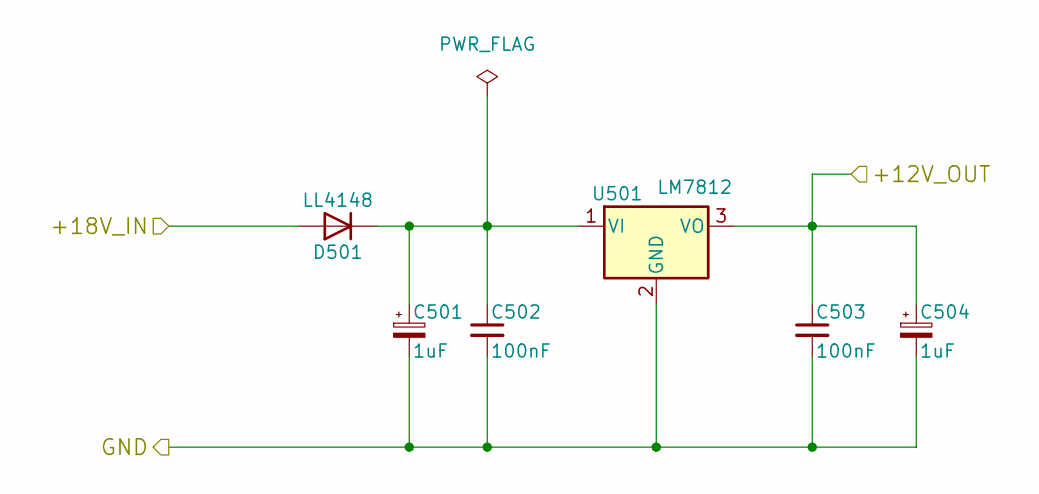
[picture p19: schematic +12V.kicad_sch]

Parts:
C501, C504: 1uF; CP_EIA-6032-20_AVX-F_Pad2.25x2.35mm_HandSolder
C502, C503: 100nF; C_0805_2012Metric_Pad1.15x1.40mm_HandSolder
D501: LL4148; D_MiniMELF_Handsoldering
U501: LM7812; TO-220-3_Horizontal_TabDown_SMD

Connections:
+12V: C503.1, C504.1, U501.3 (VO); also elsewhere on the board
unnamed: C501.1, C502.1, D501.1 (K), U501.1 (VI)
VCC: D501.2 (A); also elsewhere on the board

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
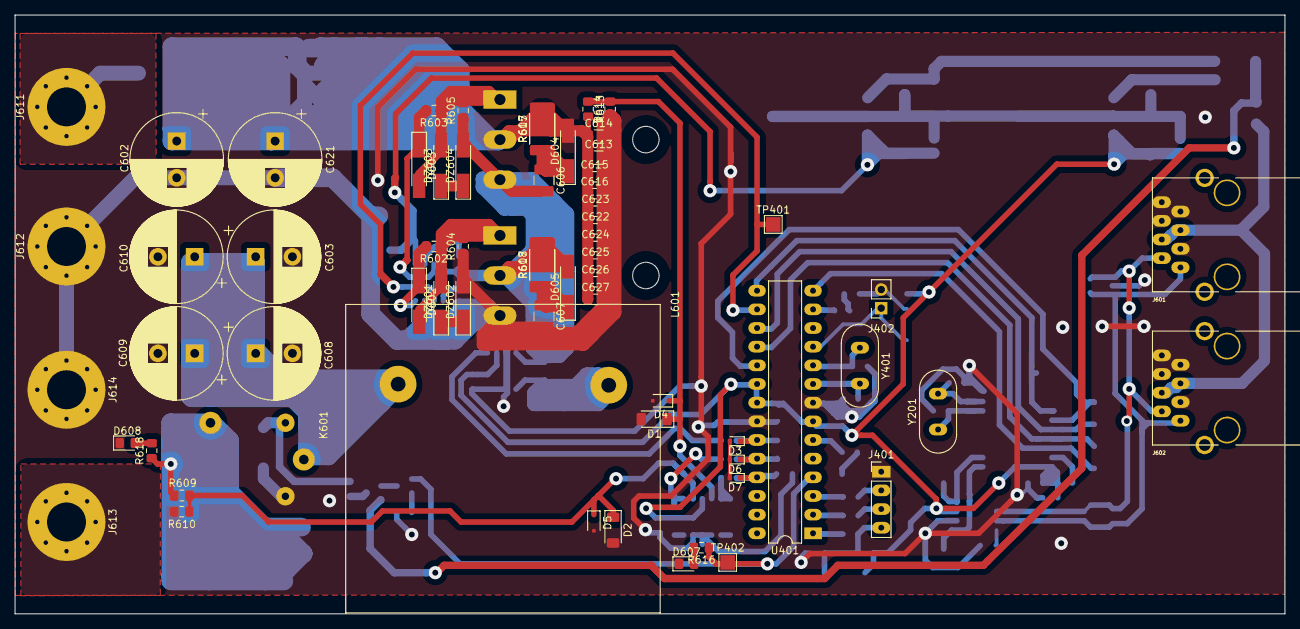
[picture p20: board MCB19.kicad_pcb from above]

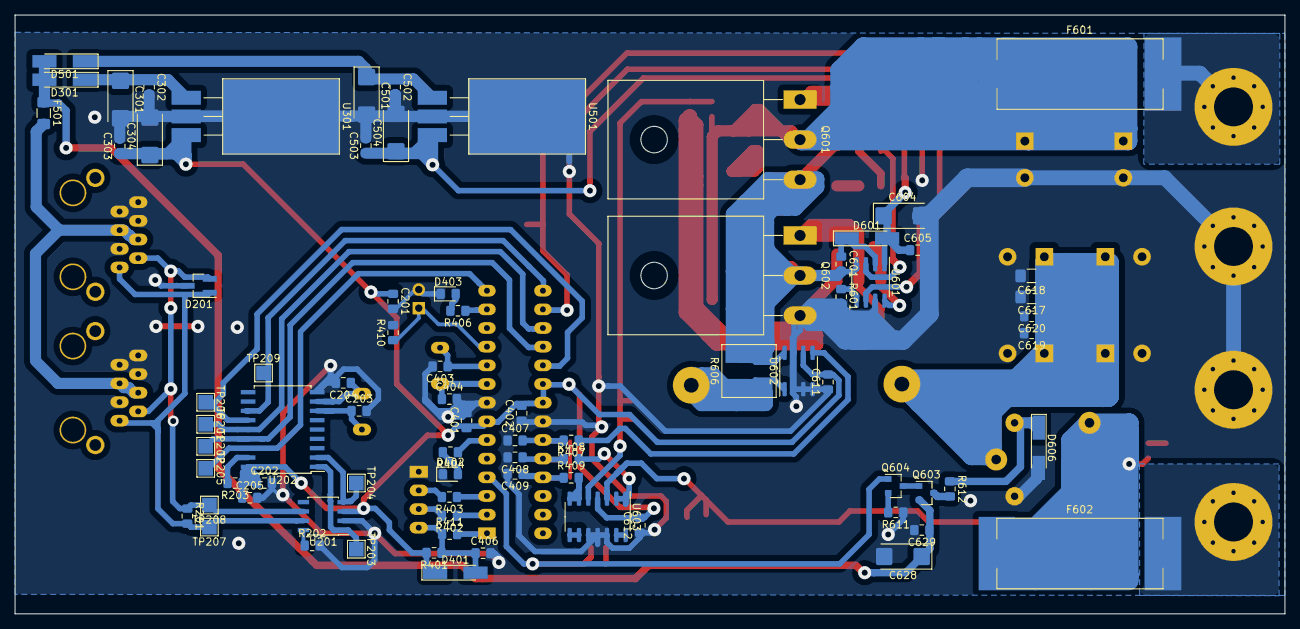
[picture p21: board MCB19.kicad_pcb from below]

Board: 2 copper layers, 172.8 x 81.5 mm, 144 parts (80 on the bottom side), 68 nets.

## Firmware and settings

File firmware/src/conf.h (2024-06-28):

/**
 * @file conf.h
 *
 * @defgroup CONF Configurations
 *
 * @brief General configuration of the system.
 *
 * @{
 */

#ifndef CONF_H
#define CONF_H

#ifndef F_CPU
#define F_CPU 16000000UL    //define a frequencia do microcontrolador - 16MHz
#endif /* ifndef F_CPU */


// CONFIGURACOES DE COMPILACAO
#define DEBUG_ON
#define VERBOSE_ON
#define VERBOSE_ON_CAN_APP
//#define VERBOSE_ON_MACHINE
//#define VERBOSE_ON_ADC
#define VERBOSE_ON_INIT
#define VERBOSE_ON_ERROR
//#define PRINT_INFOS

#define CAN_SIGNATURE_SELF      CAN_SIGNATURE_MCB19_2

// MODULES ACTIVATION
#define USART_ON
#define CAN_ON
//#define CAN_DEPENDENT
#define ADC_ON
#define MACHINE_ON
//#define LED_ON
#define WATCHDOG_ON
//#define SLEEP_ON
#define CONTROL_ON

#ifdef CONTROL_ON
#define D_MIN       0
#define D_MAX       0.9
#define VO_SETPOINT 14.6
#define IO_MAX      10
#define VO_MAX      16
#define VI_MIN      21
#define PERIOD      0.0009960853844391542f;// 0.0001995171684523453f; // 0.0002      // 5kHz
#define F_PWM       30000UL
#define PWM_DDR     DDRB
#define PWM_PIN     PINB
#define PWM_PORT    PORTB
#define PWM         PB2
#define ENABLE_RELAY  PD2
#define ENABLE_RELAY_DDR DDRD
#define ENABLE_RELAY_PIN PIND
#define ENABLE_RELAY_PORT PORTD
#endif

#ifdef MACHINE_ON
#define MACHINE_TIMER_FREQUENCY             200U           //<! machine timer frequency in Hz
#define MACHINE_TIMER_PRESCALER             1024U          //<! machine timer prescaler
#endif // MACHINE_ON

#ifdef LED_ON
#define     LED_PORT                PORTD
#define     LED_PIN                 PIND
#define     LED_DDR                 DDRD
#define     LED1                    PD7
#define     LED2                    PD7
#define     cpl_led(y)              cpl_bit(LED_PORT, y)
#define     set_led(y)              set_bit(LED_PORT, y)
#define     clr_led(y)              clr_bit(LED_PORT, y)
#else
#define     cpl_led()
#define     set_led()
#define     clr_led()
#endif // LED_ON


#ifdef CAN_ON
#define SPI_ON

// CANBUS DEFINITONS
// ----------------------------------------------------------------------------
/* Global settings for building the can-lib and application program.
 *
 * The following two #defines must be set identically for the can-lib and
 * your application program. They control the underlying CAN struct. If the
 * settings disagree, the underlying CAN struct will be broken, with
 * unpredictable results.
 * If can.h detects that any of the #defines is not defined, it will set them
 * to the default values shown here, so it is in your own interest to have a
 * consistent setting. Ommiting the #defines in both can-lib and application
 * program will apply the defaults in a consistent way too.
 *
 * Select if you want to use 29 bit identifiers.
 */
#define	SUPPORT_EXTENDED_CANID	0

/* Select if you want to use timestamps.
 * Timestamps are sourced from a register internal to the AT90CAN.
 * Selecting them on any other controller will have no effect, they will
 * be 0 all the time.
 */
#define	SUPPORT_TIMESTAMPS		0

#endif // CAN_ON

/**
 * @}
 */
 
#endif /* ifndef CONF_H */

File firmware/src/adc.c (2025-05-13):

#include "adc.h"

volatile uint8_t print_adc;

//#define ADC_8BITS
#define ADC_TIMER_PRESCALER 64
/**
 * @brief inicializa o ADC, configurado para conversão engatilhada com o timer0.
 */
void adc_init(void)
{
    clr_bit(PRR, PRADC);                           // Activates clock to adc

    // configuracao do ADC
    PORTC   =   0b00000000;                         // disables pull-up for adcs pins
    DDRC    =   0b00000000;                         // all adcs as inputs
    DIDR0   =   0b11111111;                         // digital disable for all adcs

    ADMUX   =   (0 << REFS1)                        // AVcc with external capacitor at AREF pin
            | (1 << REFS0)
#ifdef ADC_8BITS
            | (1 << ADLAR);                         // ADC left adjusted -> using 8bits ADCH only
#else
            | (0 << ADLAR);                         // ADC left adjusted -> using all 10 bits
#endif
    ADMUX = (ADMUX & 0xF8) | ADC0;                  // Choose ADMUX

    ADCSRA  =   (1 << ADATE)                        // ADC Auto Trigger Enable
            | (1 << ADIE)                           // ADC Interrupt Enable
            | (1 << ADEN)                           // ADC Enable
            | (1 << ADSC)                           // Do the first Start of Conversion
            | (1 << ADPS2)                          // ADC Prescaller = 64
            | (0 << ADPS1)
            | (1 << ADPS0);

    ADCSRB  =   (0 << ADTS2)    // Auto-trigger source: timer0 Compare Match A
            | (1 << ADTS1)
            | (1 << ADTS0);

    // TIMER configurations
    clr_bit(PRR, PRTIM0);                          // Activates clock to timer0
    // MODE 2 -> CTC with TOP on OCR1
    TCCR0A  =   (1 << WGM01) | (0 << WGM00)         // mode 2
            | (0 << COM0B1) | (0 << COM0B0)         // do nothing
            | (0 << COM0A1) | (0 << COM0A0);        // do nothing
    TCCR0B  =
#if ADC_TIMER_PRESCALER ==     1
                (0 << CS02) | (0 << CS01) | (1 << CS00) // Prescaler N=1
#elif ADC_TIMER_PRESCALER ==   8
                (0 << CS02) | (1 << CS01) | (0 << CS00) // Prescaler N=8
#elif ADC_TIMER_PRESCALER ==   64
                (0 << CS02) | (1 << CS01) | (1 << CS00) // Prescaler N=32
#elif ADC_TIMER_PRESCALER ==   256
                (1 << CS02) | (0 << CS01) | (0 << CS00) // Prescaler N=64
#elif ADC_TIMER_PRESCALER ==   1024
                (1 << CS02) | (0 << CS01) | (1 << CS00) // Prescaler N=128
#else
                0
#endif
                | (0 << WGM02);      // mode 2

    TCNT0 = 0;
    OCR0A = 82;              // OCR2A = TOP = fcpu/(N*f) -1 // Division by two only applies for toggle pin frequency.

    TIMSK0 |=   (1 << OCIE0A);          // Ativa a interrupcao na igualdade de comparação do TC0 com OCR0A

#ifdef DEBUG_ON
    set_bit(DDRD, PD5);
#endif

}

/**
 * @brief MUX do ADC
 */
ISR(ADC_vect)
{
    cli();
    static const float vi_coeff = 0.06582490575070313f;
    static const float vo_coeff = 0.06717781789490249f;
    static const float io_coeff = 0.01599315004f;

    uint16_t adc = ADC;                     // read adc
    uint8_t channel = ADMUX & 0x07;         // read channel

    /*
    cpl_bit(PORTD, PD5);
    usart_send_uint8(ADMUX);
    usart_send_char(':');
    usart_send_uint16(ADC);
    usart_send_char('\n');
    */

    switch(channel){
        case ADC0:
            io = adc * io_coeff;
            break;

        case ADC1:                       
            vo = adc * vo_coeff;
            break;

        case ADC2: default:
            vi = adc * vi_coeff;
            channel = 255;             // recycle

            print_adc = 1;
#ifdef DEBUG_ON
            set_bit(PORTD, PD5);
#endif
            control(); // call control action 
#ifdef DEBUG_ON
            clr_bit(PORTD, PD5);
#endif  
            break;
    }

    ADMUX = (ADMUX & 0xF8) | ++channel;   // select next channel
    //ADCSRA = ADCSRA;                  // rearm for next conversion if TIMER0 not in use

    sei();
}

/**
 * @brief ISR necessária para auto-trigger do ADC. Caso contrário, dispara
 * BADISR_vect.
 */
EMPTY_INTERRUPT(TIMER0_COMPA_vect);

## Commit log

2019-08-02 Criação do repositório do MCB19
    Primeiro upload de versão
    [Conectores.sch, MCB19.kicad_pcb, MCB19.sch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]
2019-08-04 Novos detalhes na placa
    Comecei a planejar onde ficam os componentes da placa, em especial os que fazem parte do buck e os que estão no atmega328p, exceto os do driver
    [MCB19.kicad_pcb, MCB19.sch, atmega328p.sch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]
2019-08-04 Mudanças no layout
    Arrumado um problema de portas trocadas
    Layout modificado no driver
    Proxima parte: Adicionar filtros para as medidas
    [MCB19.kicad_pcb, MCB19.sch, atmega328p.sch]
2019-08-05 simulations for driver and buck added
2019-08-05 Parametros da simulação transposta para .params
2019-08-06 Novo design
    Foi realizada uma nova topologia para a placa, diminuindo trilhas de alta importância
    Ainda faltam algumas partes do circuito
    [MCB19.kicad_pcb]
2019-08-11 Snubber funcionando, mas buck contém erros
2019-08-12 Final
    Design de layout pronto
    [MCB19.kicad_pcb, atmega328p.sch, driver.sch]
2019-08-12 Final refeito Remodelagem de trilhas e acertos de distancias Sera necessario uma verificação das malhas
    [MCB19.kicad_pcb]
2019-08-12 Verificação de trilhas na regiao do indutor OK
    [MCB19.kicad_pcb]
2019-08-13 Terminando os detalhes ajustes de malha e trilha tem que ser verificado
    [MCB19.kicad_pcb]
2019-08-23 Mudança nas trilhas para melhor funcionamento
    Detalhes finais para a fabricação
    [MCB19.kicad_pcb, MCB19.sch, atmega328p.sch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]
2019-08-26 Final!!!
    Pronto para fabricar
    [MCB19.kicad_pcb, MCB19.sch, driver.sch]
2019-08-29 Capacitor corrigido
    Havia um capacitor com medidas erradas, que já foram corrigidas.
    Para o protótipo já desenvolvido, não ha problemas pois há espaço para a correção.
    [MCB19.kicad_pcb]
2019-10-07 New version
    Detalhes
    [+15V.sch, MCB19.kicad_pcb, MCB19.sch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]
2019-10-24 Versão 2.0
    Novas modificações, após confirmado, pode ser fabricada
    [MCB19.kicad_pcb, driver.sch, supplies.sch]
2019-10-24 Versão 2.1
    Tinha uma trilha com problema
    [MCB19.kicad_pcb]
2019-10-25 Versão 2.2
    Funcional, com a centralização dos mosfets, e a aplicação de um DRC para garantia de funcionamento
    [MCB19.kicad_pcb]
2019-10-26 Esquemático corrigido, layout retrabalhado.
    No esquemático foram adicionados alguns capacitores para os opamps e aumentado a quantidade de capacitores na saída. Alguns detalhes de regras elétricas relacionadas aos PWR_FLAGs foram corrigidos.
    Para o layout, na tentativa de encontrar um roteamento mais simples e claro, no qual fosse possível desenhar o caminho das correntes das malhas, utilizando o PMP7165 da Texas Instruments como referência.
    [MCB19.kicad_pcb]
2019-10-26 trilhas aumentadas para 30mils
    [MCB19.kicad_pcb]
2019-10-26 3D added
    [MCB19-B_Adhes.gbr, MCB19-B_CrtYd.gbr, MCB19-B_Cu.gbr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]
2019-10-26 3D updated
    [MCB19.kicad_pcb]
2019-10-26 Snubber and shunt footprints fixed
    [MCB19-B_Adhes.gbr, MCB19-B_CrtYd.gbr, MCB19-B_Cu.gbr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]
2019-10-30 ready for fab
    [MCB19-B_Adhes.gbr, MCB19-B_CrtYd.gbr, MCB19-B_Cu.gbr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]
2019-11-07 fabs updated with drill holes
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2020-01-15 enable, vi, vo
    [+15V.sch, MCB19.kicad_pcb, MCB19.sch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]
2020-01-15 Adição das mudanças pré-DSB(SF) feitas no MCB19
    [+15V.sch, MCB19.kicad_pcb, MCB19.sch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]
2020-01-15 checkpoint. Serious problems with ADC. :(
    [adc.c, conf.h]
2020-01-15 adc & control working
2020-01-16 small fixes in layout. Fabrication files exported.
    [+15V.sch, MCB19.kicad_pcb, MCB19.sch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]
2020-01-16 simulations for enable for driver and mosfet added
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2020-01-19 driver better referenced to low-side mosfet
    [+12V.sch, MCB19.kicad_pcb, MCB19.sch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]
2020-01-20 relay driver almost finished
    [MCB19.kicad_pcb]
2020-01-21 relay finished
    [MCB19.kicad_pcb, MCB19.sch, driver.sch]
2020-01-21 new logic for controller, using relay
2020-01-22 Some fixes, ready for heat transfering
    [+12V.sch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]
2020-01-22 relay pin 1 fixed
    [MCB19.kicad_pcb, MCB19_panel.kicad_pcb]
2020-01-22 some necks removed
    [MCB19.kicad_pcb, MCB19_panel.kicad_pcb]
2020-01-22 references added to pdf
    [MCB19_panel.kicad_pcb]
2020-01-29 incluido envio da tensao de saida
2020-07-13 export 3D and layout images
    [MCB19.kicad_pcb]
2020-07-29 Add image of current limitting simulation
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2020-08-07 Fix Doxygen start end end of defgroups
    [conf.h]
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2020-08-13 Clean unecessary files
    [MCB19-B_Adhes.gbr, MCB19-B_CrtYd.gbr, MCB19-B_Cu.gbr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]
2020-08-13 Fix bom separator
2020-08-13 Add html bom and fix output names
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2020-08-14 Fix gerbers
2020-08-19 Fix multiple symbol definitions using externs
    [adc.c]
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2020-10-20 ci: bump nerdyscout/kicad-exports from v2.0 to v2.1 (#18)
    Bumps [nerdyscout/kicad-exports](https://github.com/nerdyscout/kicad-exports) from v2.0 to v2.1.
    - [Release notes](https://github.com/nerdyscout/kicad-exports/releases)
    - [Changelog](https://github.com/nerdyscout/kicad-exports/blob/60350fc060ef3057fe6a3565357c6a9a8952f9cf/CHANGELOG.md)
    - [Commits](https://github.com/nerdyscout/kicad-exports/compare/v2.0...60350fc060ef3057fe6a3565357c6a9a8952f9cf)
2020-10-21 Revert "ci: bump nerdyscout/kicad-exports from v2.0 to v2.1 (#18)" (#20)
    This reverts commit 56917f199afc0ef314f368c75055a4ef2152a35f.
2020-10-23 ci: bump nerdyscout/kicad-exports from v2.0 to v2.1 (#21)
    * ci: bump nerdyscout/kicad-exports from v2.0 to v2.1
    - [Changelog](https://github.com/nerdyscout/kicad-exports/blob/master/CHANGELOG.md)
    * Fix pcbdraw path
    "/opt/pcbdraw/pcbdraw" -> "/opt/pcbdraw"
    * Add config files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
2020-11-16 ci: bump nerdyscout/kicad-exports from v2.1 to v2.2 (#22)
    Bumps [nerdyscout/kicad-exports](https://github.com/nerdyscout/kicad-exports) from v2.1 to v2.2.
    - [Commits](https://github.com/nerdyscout/kicad-exports/compare/v2.1...4c23c0b2fd2f25ed36da3b85af3394ac87bb9c3c)
    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
2021-04-06 ci: bump nerdyscout/kicad-exports from v2.2 to v2.3 (#29)
    Bumps [nerdyscout/kicad-exports](https://github.com/nerdyscout/kicad-exports) from v2.2 to v2.3.
    - [Changelog](https://github.com/nerdyscout/kicad-exports/blob/7f9a3e4e2c0c34a690d120f58cf43cb6c2356a53/CHANGELOG.md)
    - [Commits](https://github.com/nerdyscout/kicad-exports/compare/v2.2...7f9a3e4e2c0c34a690d120f58cf43cb6c2356a53)
    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
2021-04-07 Revert "ci: bump nerdyscout/kicad-exports from v2.2 to v2.3 (#29)" (#32)
    This reverts commit a5d21faea9a94bb788901ace415ef9d2aff880d7.
2021-04-28 ci: bump nerdyscout/kicad-exports from v2.2 to v2.3 (#33)
    - [Changelog](https://github.com/nerdyscout/kicad-exports/blob/main/CHANGELOG.md)
    - [Commits](https://github.com/nerdyscout/kicad-exports/compare/v2.2...57ab68d2d60ce7cbff1c92e309980a363ced9580)
    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
2021-04-28 Fix wrong output dir for boardview
2022-03-19 Improve voltage transient on rapid load changes, change setpoint to 14V.
2023-07-31 Fixed to new ids and added empiracally new frequency
    [conf.h]
2024-06-29 Fix wrong print function: Should be u16, not float
2025-05-06 Mudança na leitura de Vin
    [+12V.kicad_sch, MCB19.kicad_pcb, MCB19.kicad_sch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]
2025-05-09 Schematic organization improvement, use <driver> sheet as example
    [+12V.kicad_sch, MCB19.kicad_pcb, MCB19.kicad_sch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]
2025-05-13 correct equation for compare event, different than pin toggling!
    [adc.c]
2025-05-13 add diode protections for Vsense OpAmps and uC port
    [MCB19.kicad_sch, atmega328p.kicad_sch, driver.kicad_sch]
2025-05-16 Atualiza layout PCB e arquivos de produção
    [MCB19-B_Adhesive.gbr, MCB19-B_Courtyard.gbr, MCB19-B_Cu.gbr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]
